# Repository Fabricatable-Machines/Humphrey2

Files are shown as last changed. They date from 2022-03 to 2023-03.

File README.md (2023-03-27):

# Humphrey2
A self replicating large format open hardware CNC router

*by Jens Dyvik, March 2022 - ongoing*

### Index

 - [Dev log](https://github.com/Fabricatable-Machines/Humphrey2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)
 - [Bill of materials](https://github.com/Fabricatable-Machines/Humphrey2#bom)
 - [FreeCAD source file](https://github.com/Fabricatable-Machines/Humphrey2/blob/main/humphrey2.FCStd)
 - [STEP export of assembly](https://github.com/Fabricatable-Machines/Humphrey2/blob/main/humphrey2-step-export.step)
 - [Files for CNC milling](https://github.com/Fabricatable-Machines/Humphrey2/tree/main/files-for-CNC-machining)
 - [Files for 3D printing](https://github.com/Fabricatable-Machines/Humphrey2/tree/main/files-for-3D-print)
 - [License](https://github.com/Fabricatable-Machines/Humphrey2#license)

### Dev log March 27th 2023 - Self-replication test and family tree

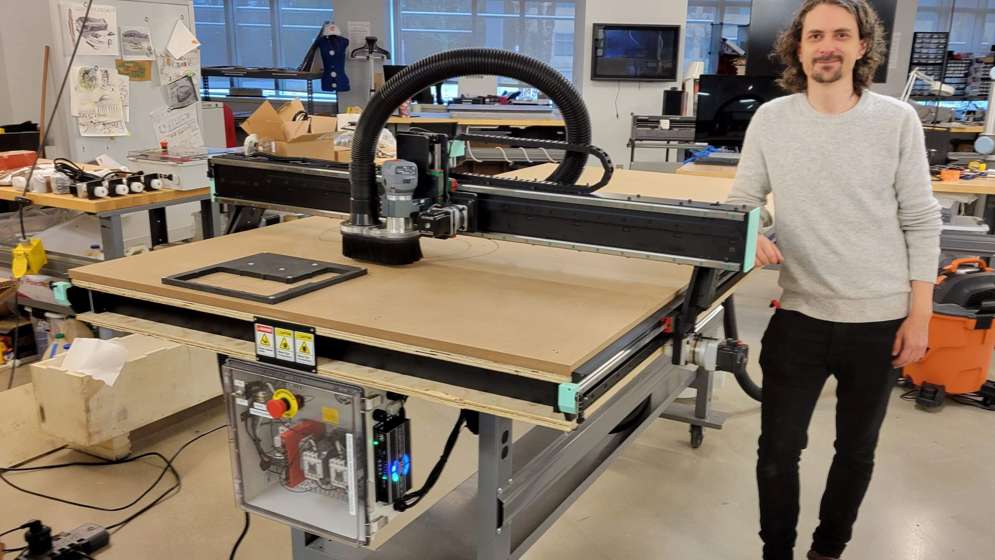
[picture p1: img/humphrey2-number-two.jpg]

*An assembled and operational Humphrey2 made on a Humphrey2*

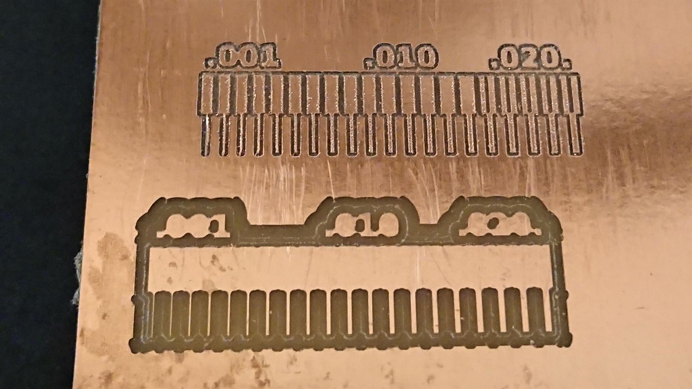
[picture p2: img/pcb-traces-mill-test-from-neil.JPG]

*Precicion test. Feature size in inches. Very low backlash and high repeatability. Unfortunately the only available 0.4mm end mill was broken, so the top traces are rough*


*The machine family tree so far. Three generations of machines making machines.*

### Dev log November 29th 2022 - Good test cuts and promising self-replication

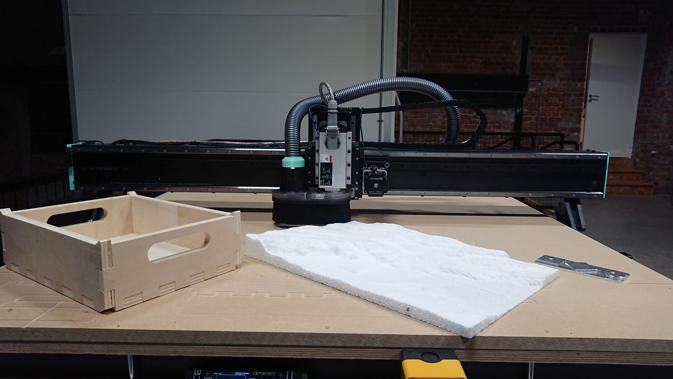
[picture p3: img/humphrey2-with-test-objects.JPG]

*15mm poplar plywood cut in one pass at 4200mm/m, 50mm styrofoam 3D milled and 8mm aluminium test pattern*

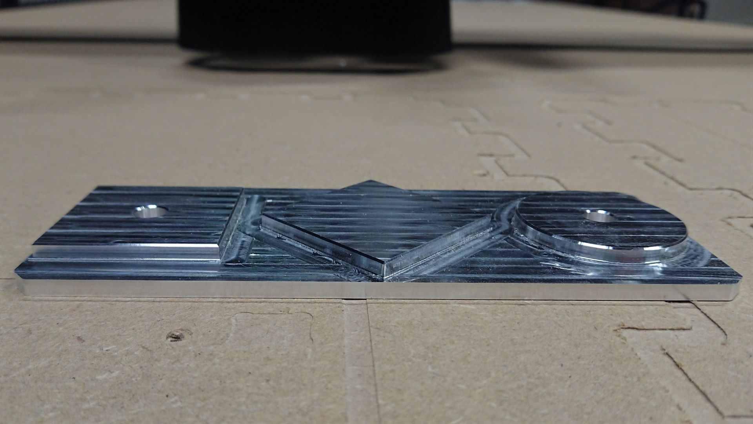
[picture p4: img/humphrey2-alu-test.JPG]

*Accuracy seems to be about +- 0.1mm. 6082 Aluminium cut with a 6mm single flute bit. 0.7mm pass depth, 1440mm/m feedrate + finish pass*

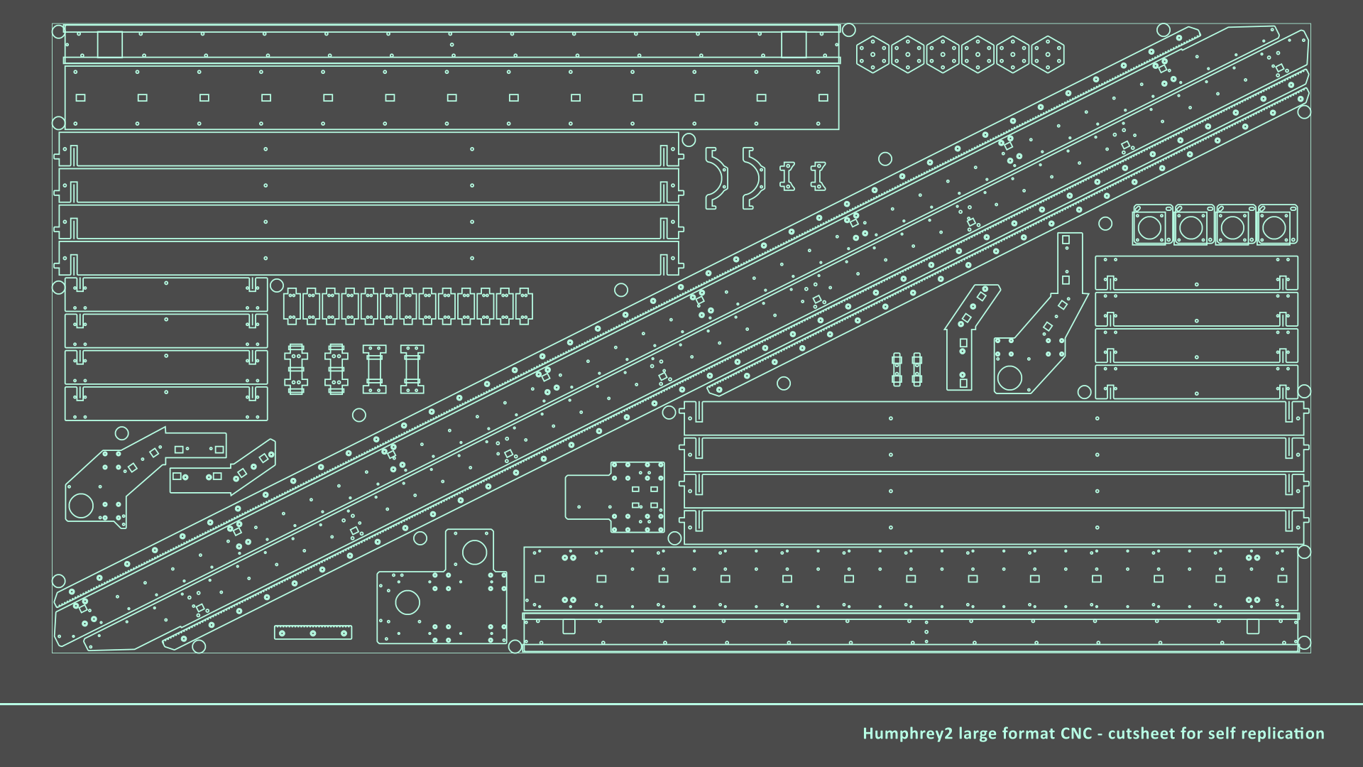
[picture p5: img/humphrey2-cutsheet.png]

*All phenolic parts for a Humphrey2 fit on one 2440mm x 1220mm x12mm sheet. The same size as the work area.*

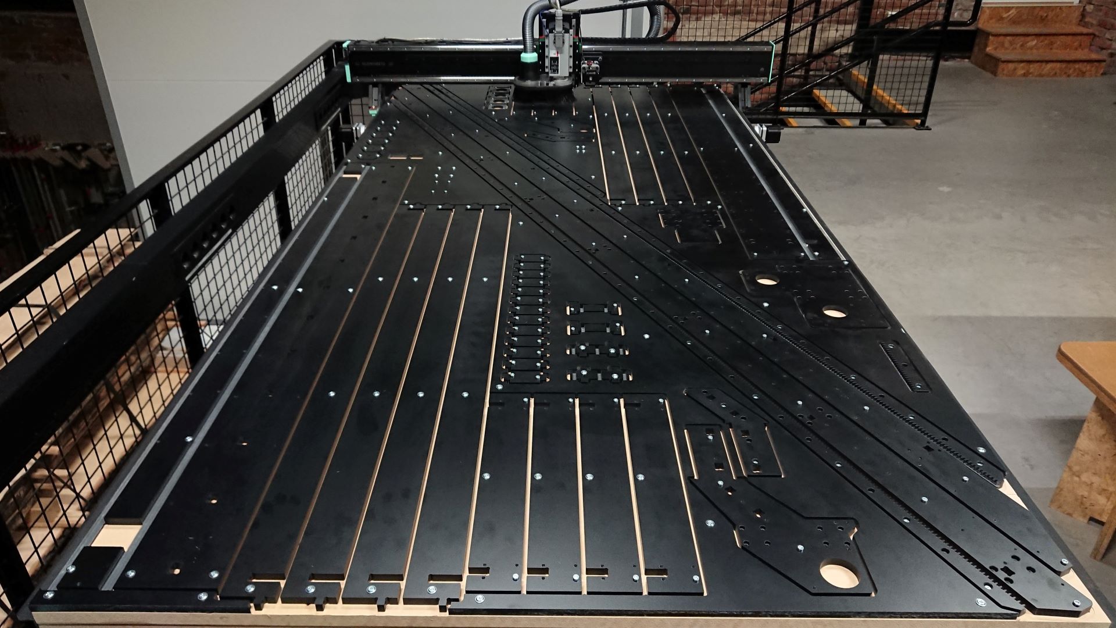
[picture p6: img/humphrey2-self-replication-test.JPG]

*Test milling of parts went well*

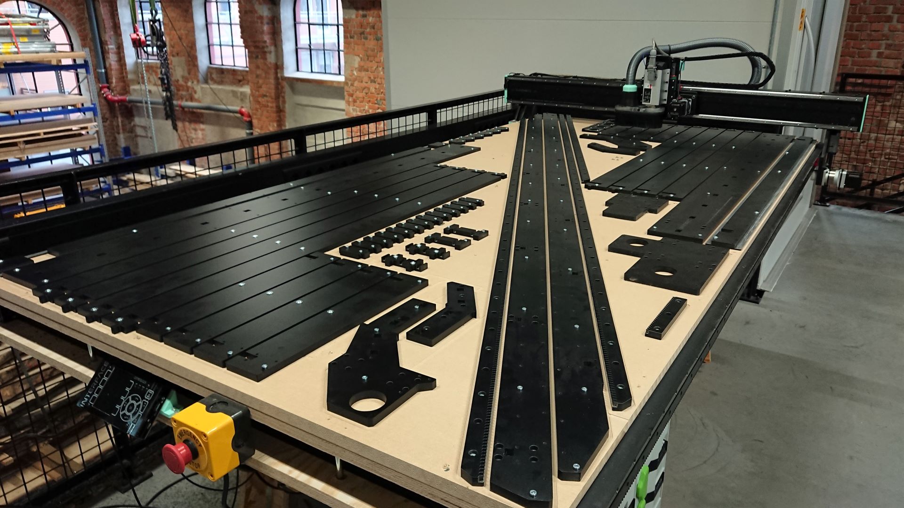
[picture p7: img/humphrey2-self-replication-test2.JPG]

*Cutsheet with all the leftover material removed. Note all the screws holding down each part allowing for a finish pass*

### Dev log October 31st 2022 - Smooth sailing for first test milling of parts and assembly

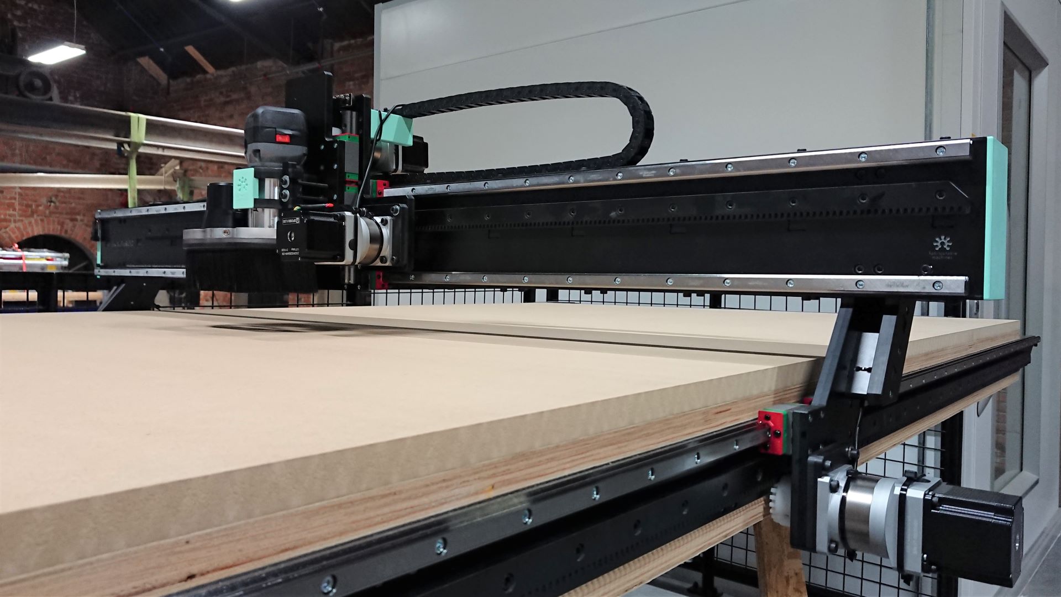
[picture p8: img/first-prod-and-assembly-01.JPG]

*Very few hickups during first assembly - next up lots of testing*

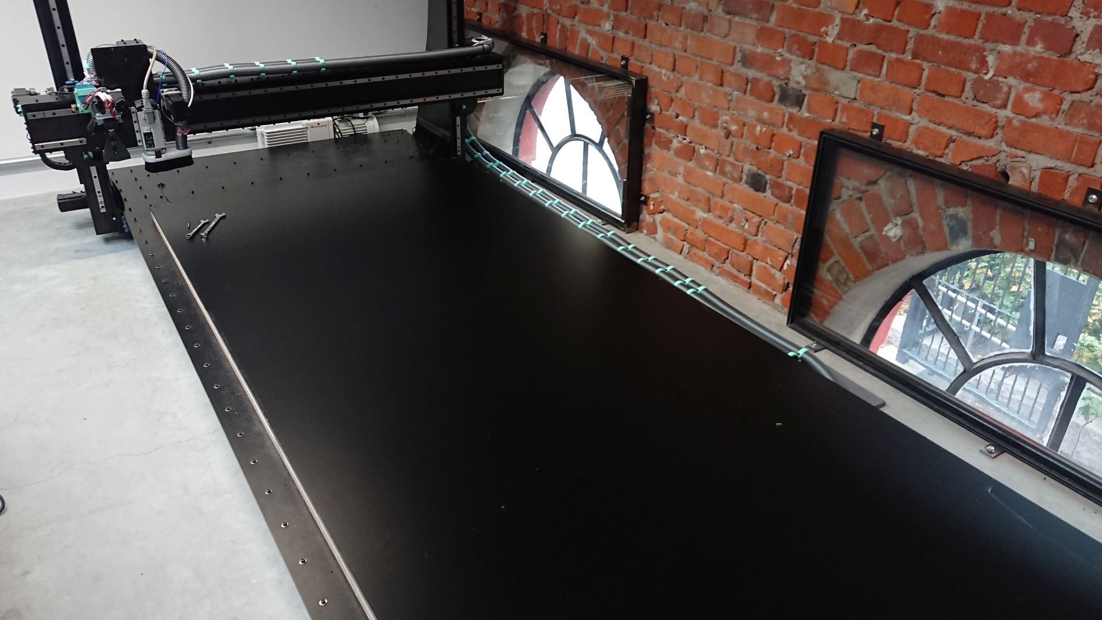
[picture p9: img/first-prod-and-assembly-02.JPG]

*Full size phenolic sheet loaded on [Hanzo](https://github.com/Fabricatable-Machines/Hanzo), ready to become Humphrey2 parts*

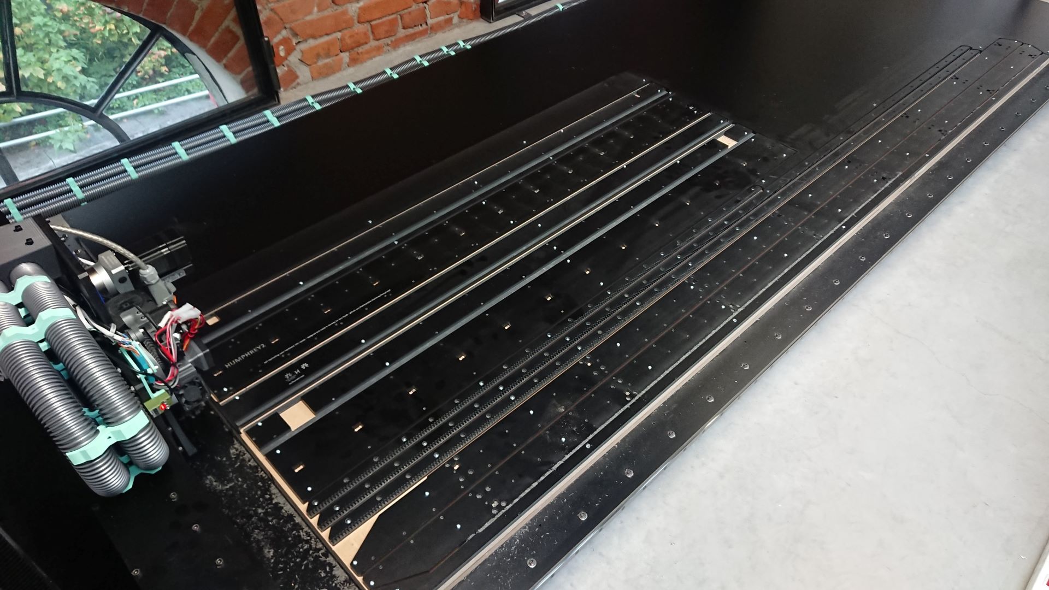
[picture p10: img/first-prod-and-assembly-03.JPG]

*It felt great to use [Hanzo](https://github.com/Fabricatable-Machines/Hanzo), a Fabricatable machine, to make another Fabricatable machine!*

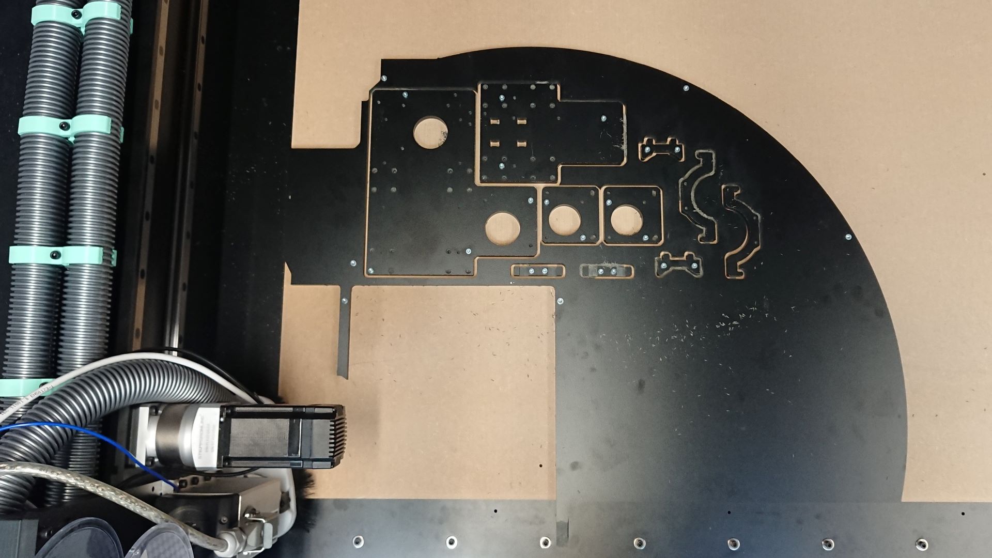
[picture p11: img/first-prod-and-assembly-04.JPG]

*Using leftovers to make X - Z assembly parts*

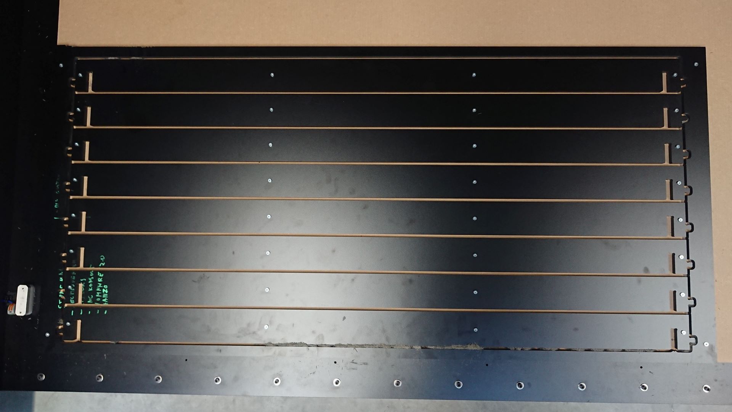
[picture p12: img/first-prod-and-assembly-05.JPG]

*The cross pieces were also milled from leftovers*

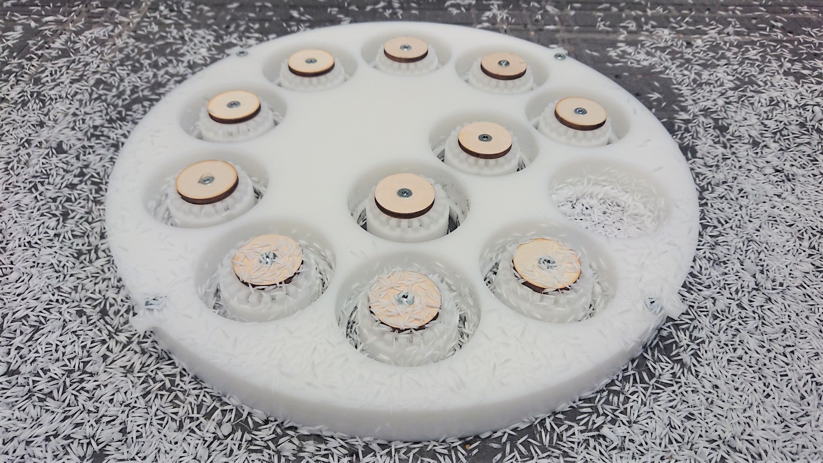
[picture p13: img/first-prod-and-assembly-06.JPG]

*Batch milling pinions from POM plastic leftovers*

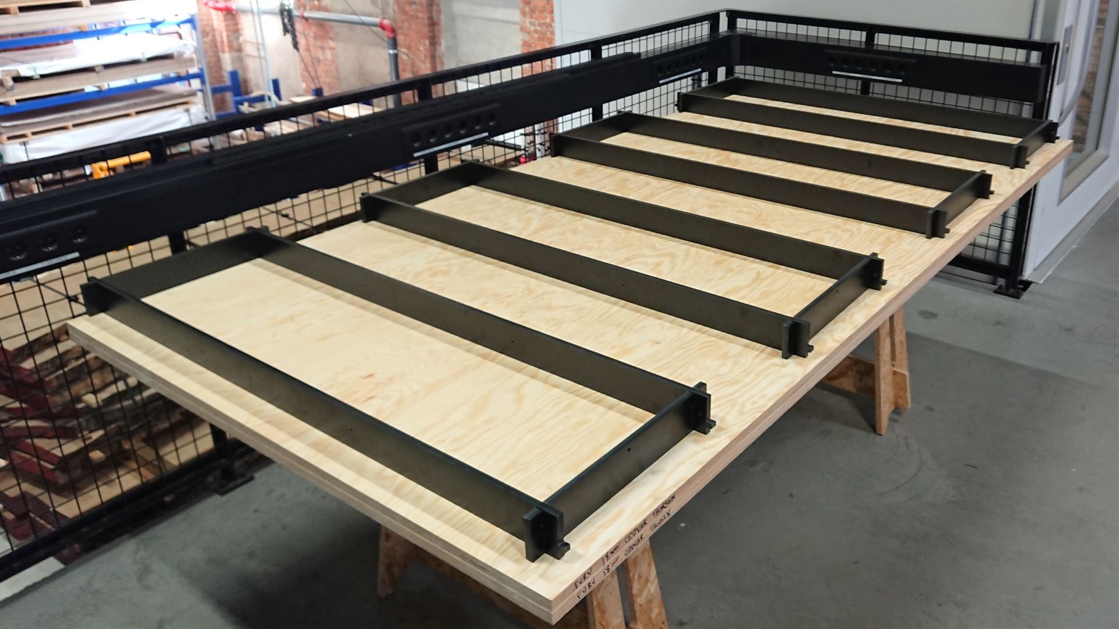
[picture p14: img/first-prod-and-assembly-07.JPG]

*The cross pieces ensure constant distance between the left and right X rail, and function as torsion box spacers*

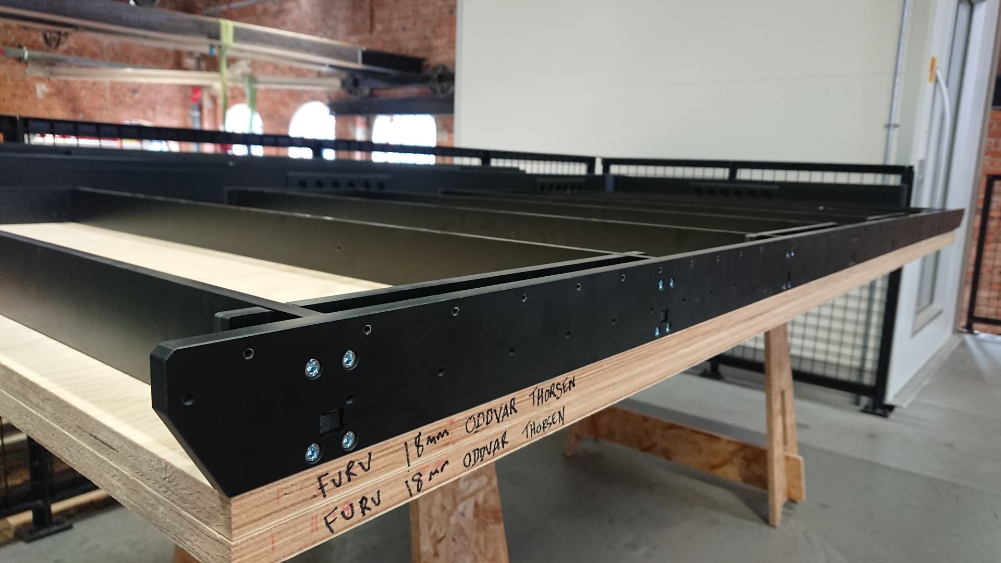
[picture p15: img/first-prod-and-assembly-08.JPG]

*All holes thread milled during production makes assembly fast*

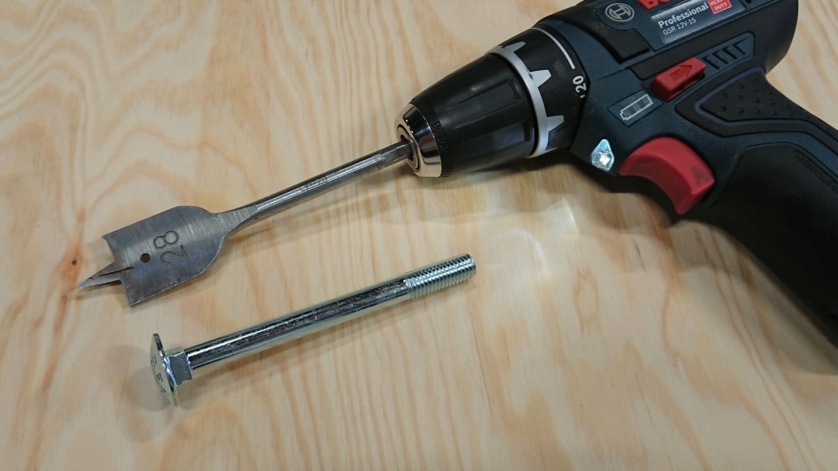
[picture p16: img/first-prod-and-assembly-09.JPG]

*Using a spade drill to counterbore the carriage bolt holes*

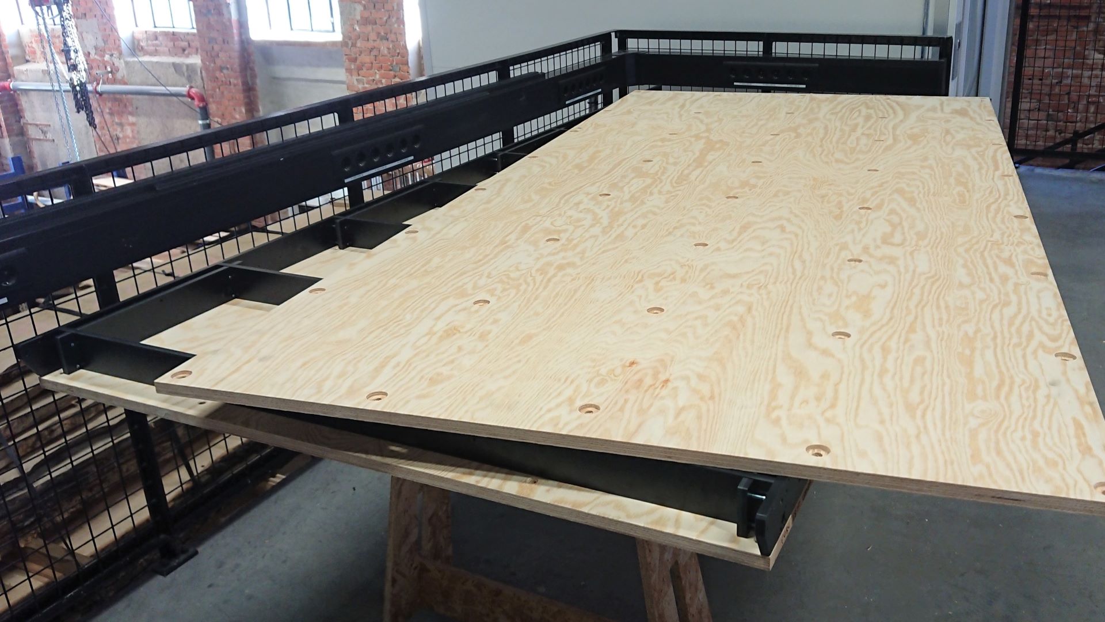
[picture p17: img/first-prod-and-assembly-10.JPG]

*The two plywood sheets that make up the top and bottom torsion box skin of the bed can be drilled manually on site. This makes for cheaper and easier shipping of the milled parts.*

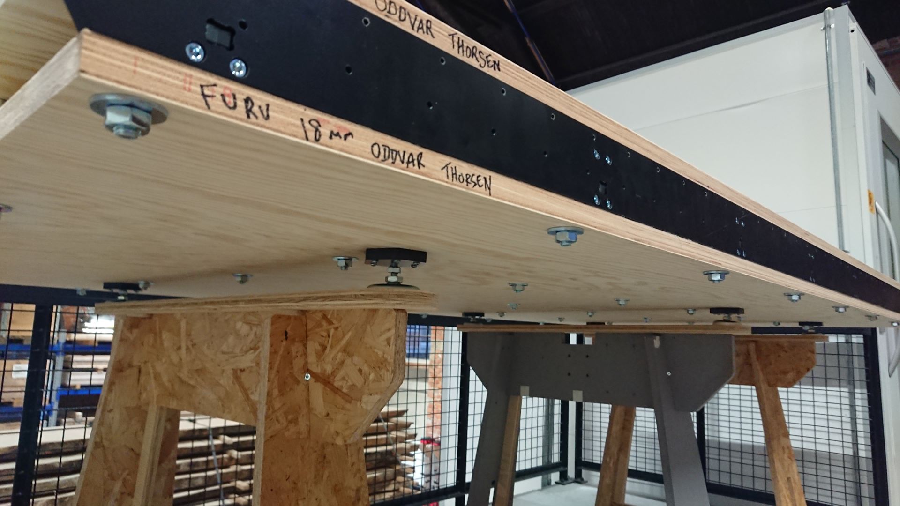
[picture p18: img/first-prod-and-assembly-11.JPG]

*The adjustable feet enable leveling. What kind of sawhorse or legs to use is open.*

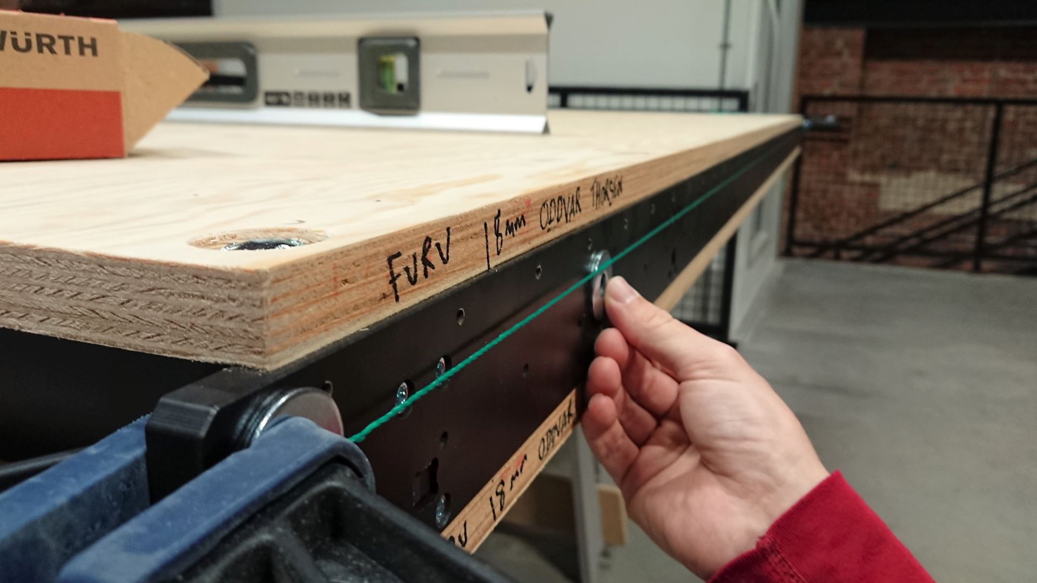
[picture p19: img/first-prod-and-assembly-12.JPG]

*Using masonry thread and three washers to make the outer walls carrying the X rails as straight as possible. As spirit level is used to try to make the assembly flat.*

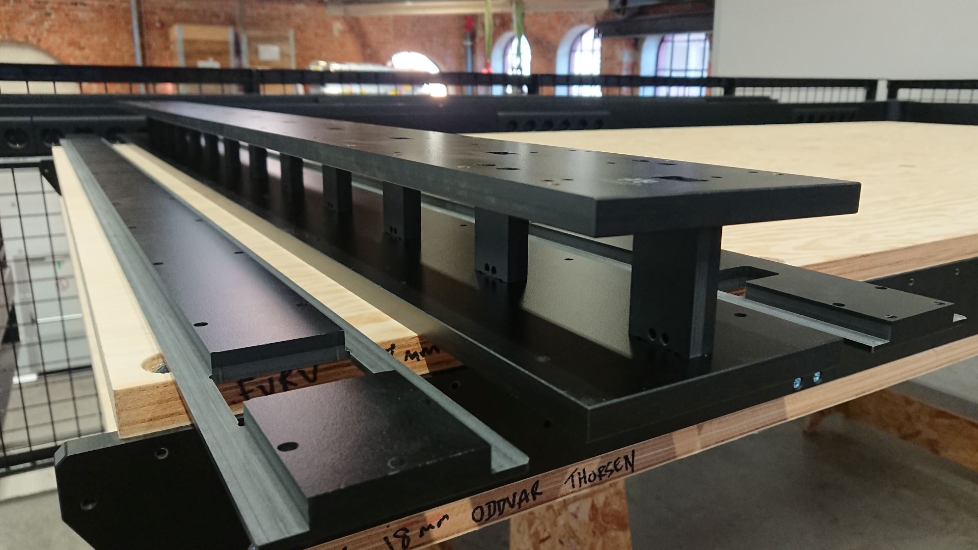
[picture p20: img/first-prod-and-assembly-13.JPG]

*The gantry has spacer nuts so shorter screws can be used*

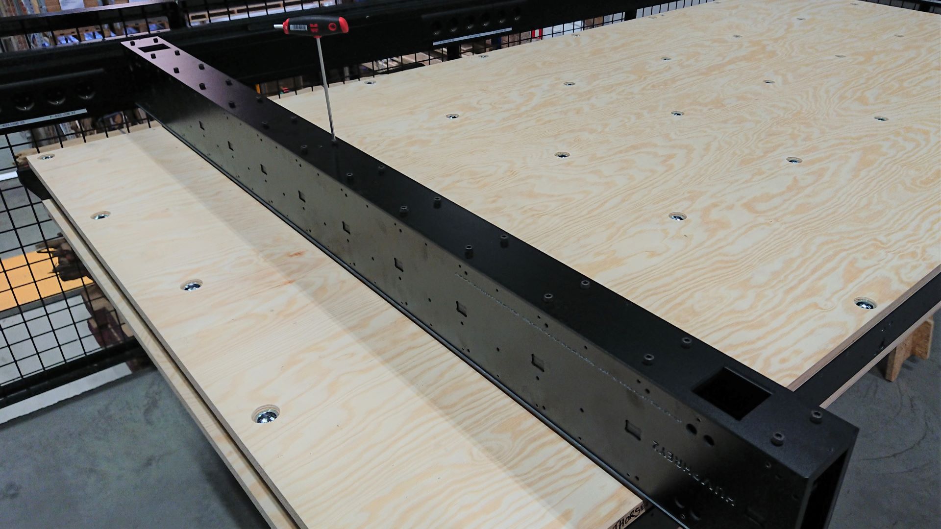
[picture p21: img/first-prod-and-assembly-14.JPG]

*Again, all holes thread milled during manufacturing makes assembly super fast*

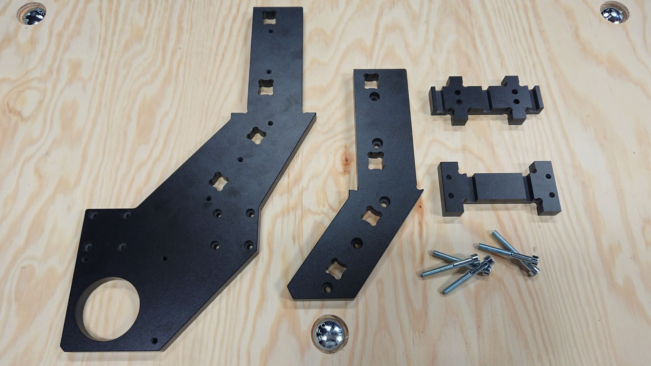
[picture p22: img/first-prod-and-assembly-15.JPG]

*Gantry feet parts*

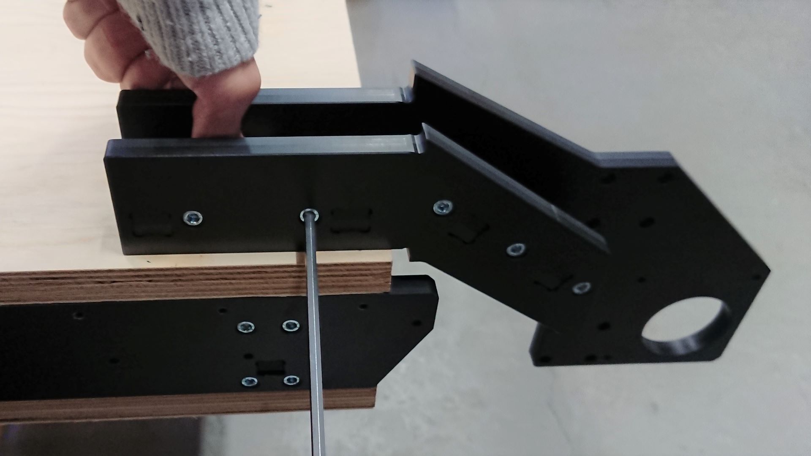
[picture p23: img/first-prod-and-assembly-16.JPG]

*Tightening under pressure*

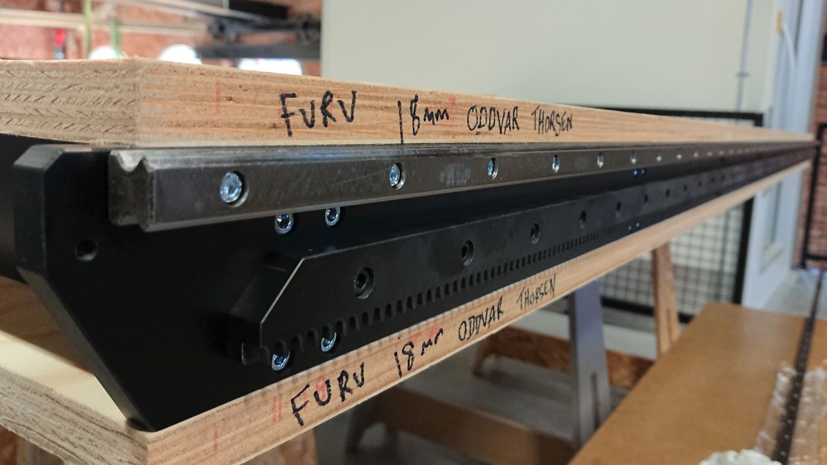
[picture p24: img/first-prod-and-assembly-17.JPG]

*Mounting rails and racks*

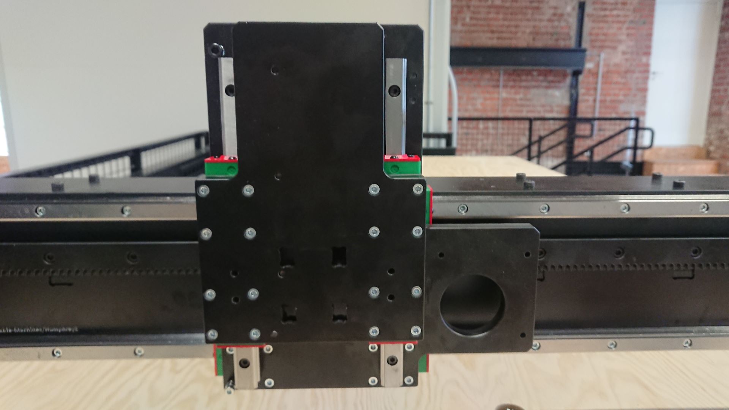
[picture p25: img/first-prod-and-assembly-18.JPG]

*Mounting the X-Z carriage*

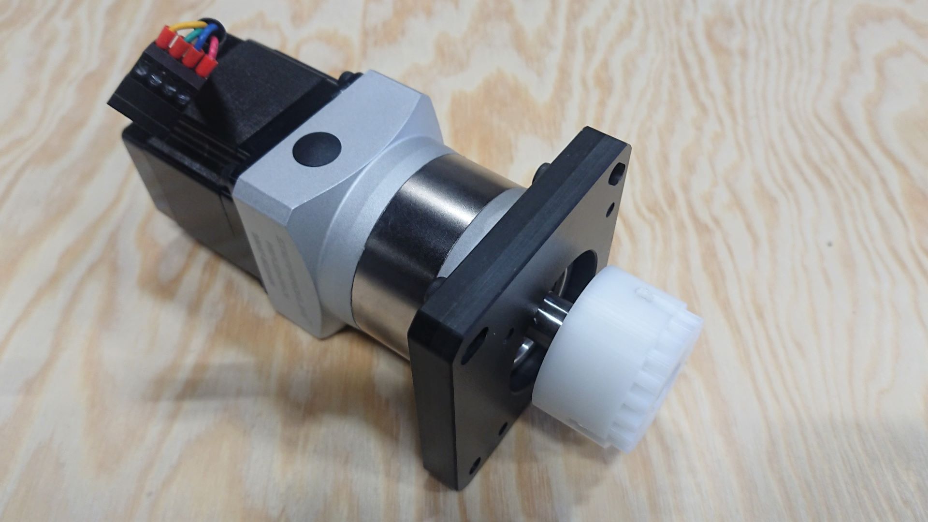
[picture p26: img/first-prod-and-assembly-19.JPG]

*Mounting gearboxes to the steppers and pinion and motor plates to the gearboxes*

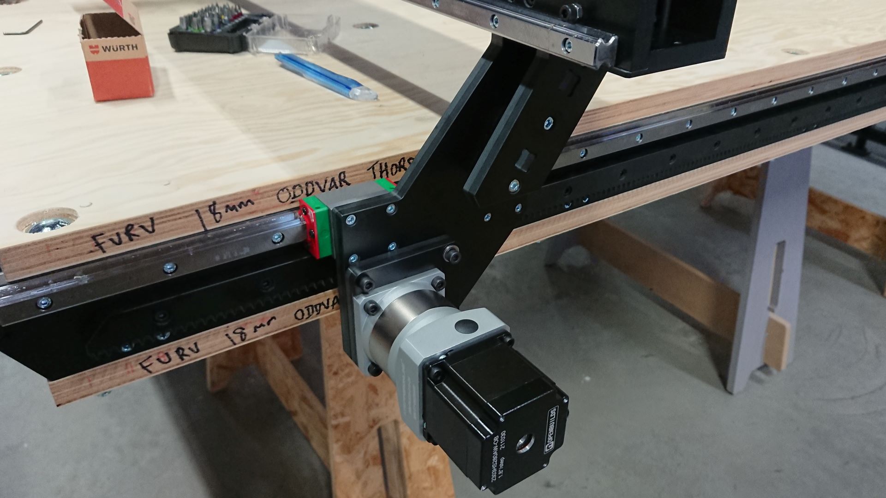
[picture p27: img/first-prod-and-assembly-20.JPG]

*Gantry detail. The pinions should be snug but not too tight against the racks.*

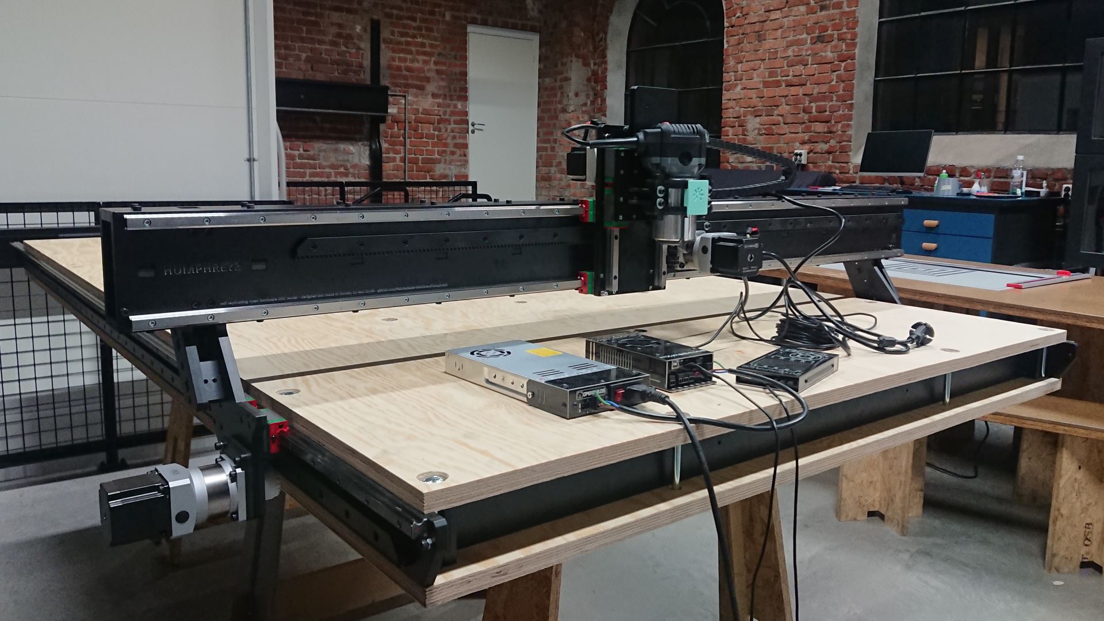
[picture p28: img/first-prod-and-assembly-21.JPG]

*Preparing for electronics work. I am testing the OpenBuilds Blackbox and Interface for fast and easy wiring.*

### Dev log October 4th 2022 - Nesting done + design tweaks

Next up; machining, assembly and testing!

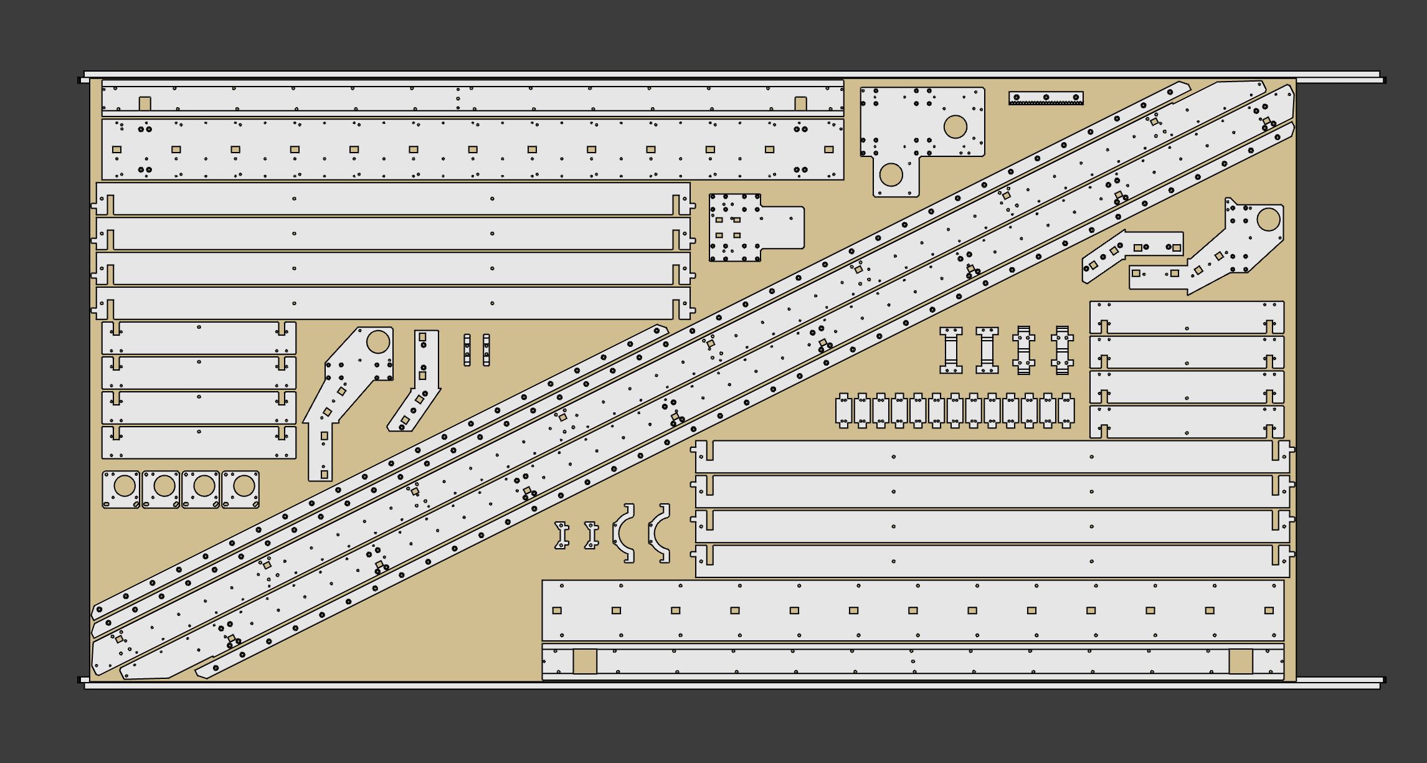
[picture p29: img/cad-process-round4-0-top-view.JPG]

*59 parts to machine from phenolic resin composite, all from a single cutsheet*

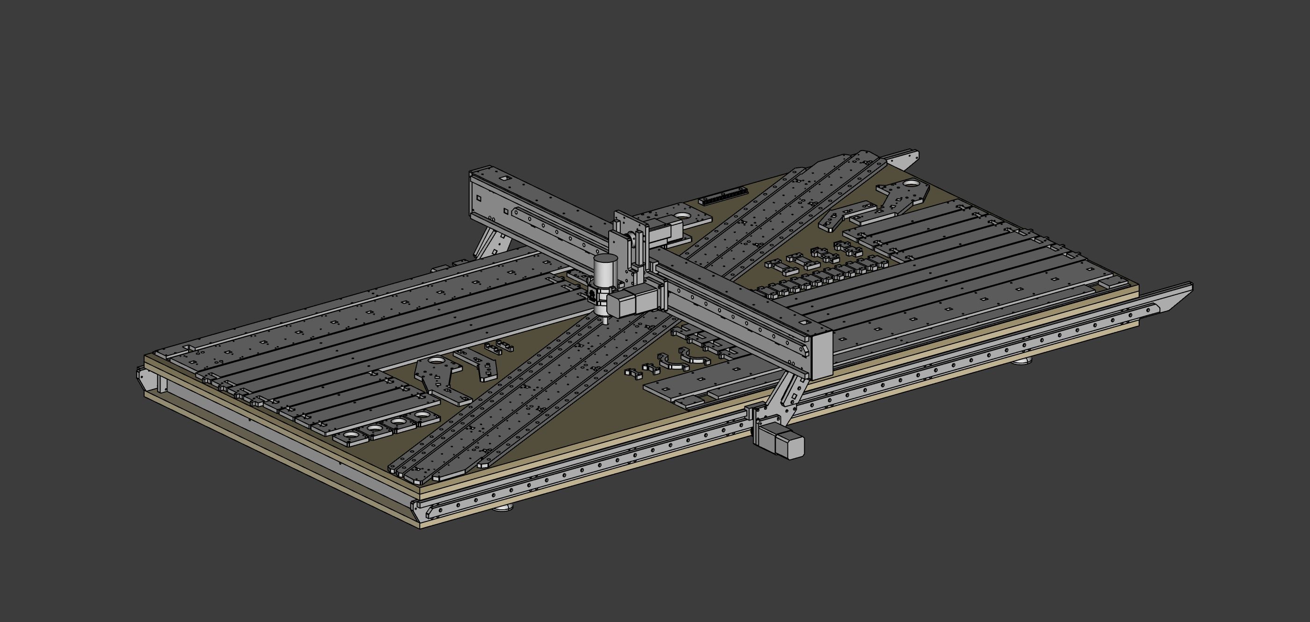
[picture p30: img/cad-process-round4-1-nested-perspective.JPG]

*Portrait of a self replicating machine*

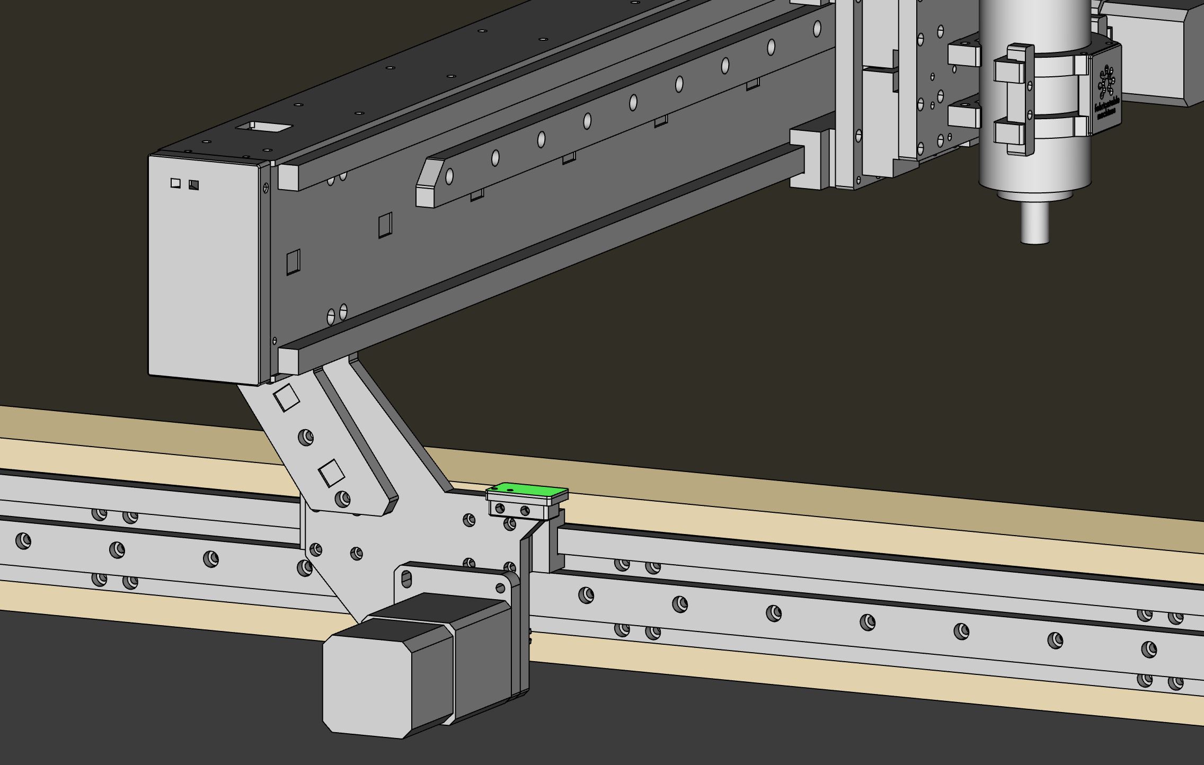
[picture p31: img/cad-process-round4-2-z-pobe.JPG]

*Added probe plate for Z axis probing of bit length*

### Dev log September 9th 2022 - Initial design is done!

Finally the first version of the design is done. The FreeCAD model is fully parametric, which feels great. So it is possible to change parameters like material thickness, tolerances, clearance between the gantry and the bed and so on without breaking the model. Next up is test milling some parts and maybe do some parameter tuning before milling all the parts for the first prototype!

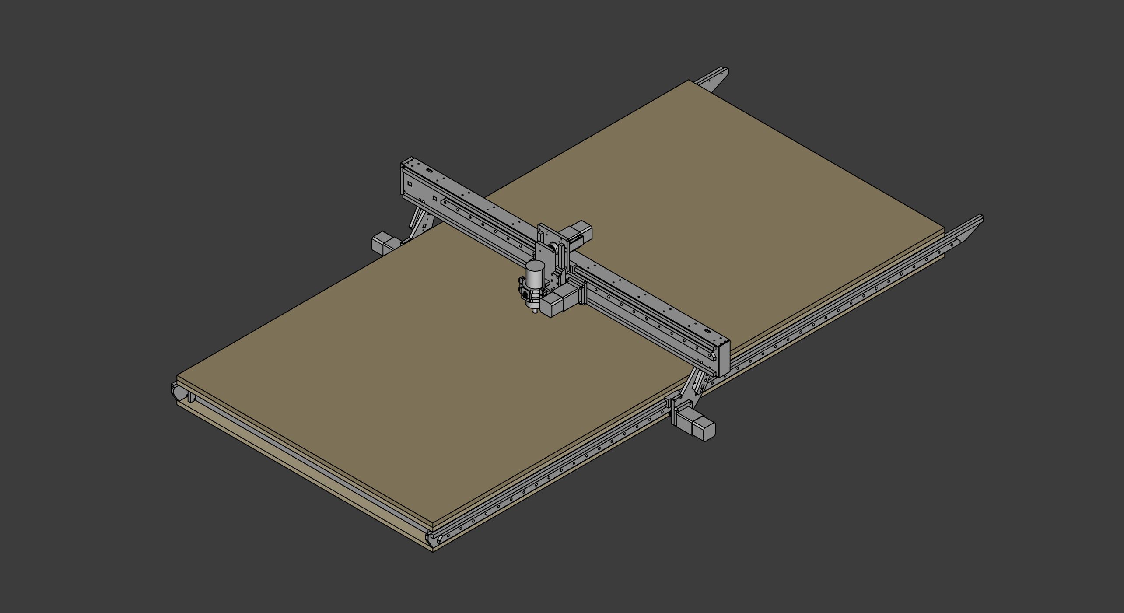
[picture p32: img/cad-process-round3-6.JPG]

*Proportions feel good*

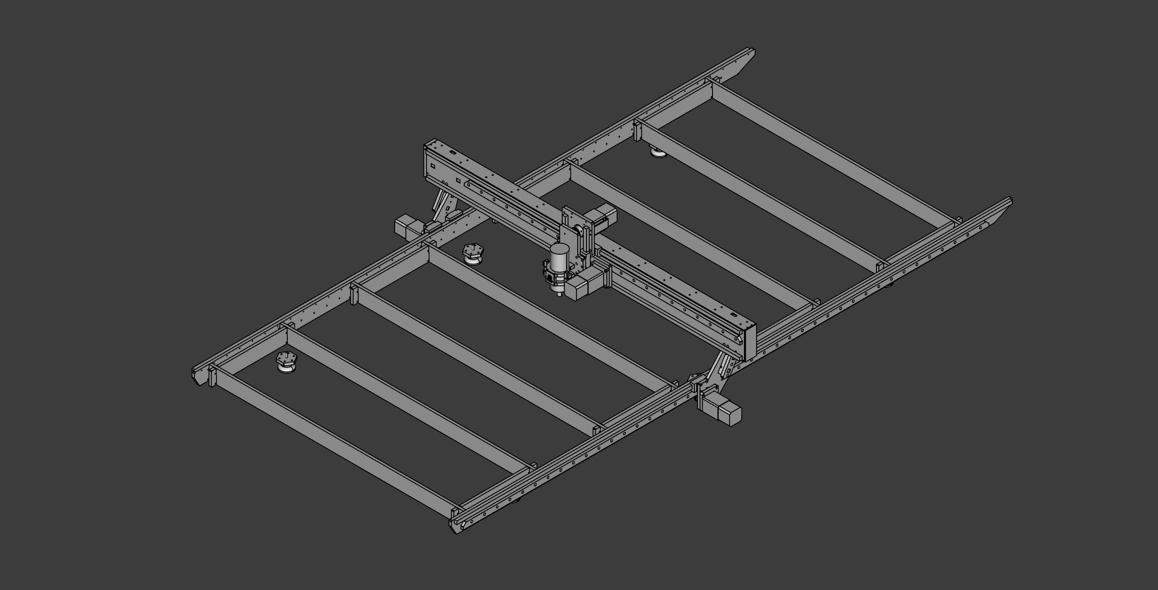
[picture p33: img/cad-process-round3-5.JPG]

*The skeleton without the plywood torsion box skins and the sacrificial MDF layer*

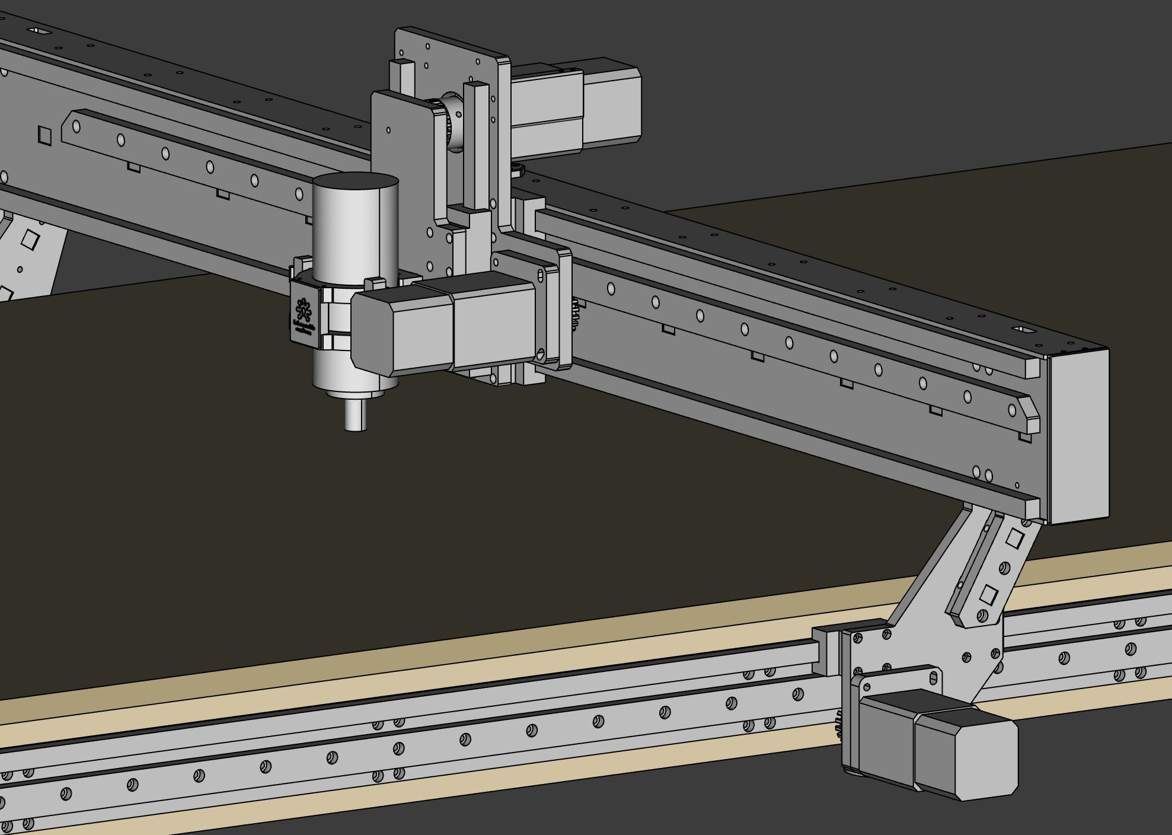
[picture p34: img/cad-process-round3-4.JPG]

*Close up of the gantry and XZ axis*

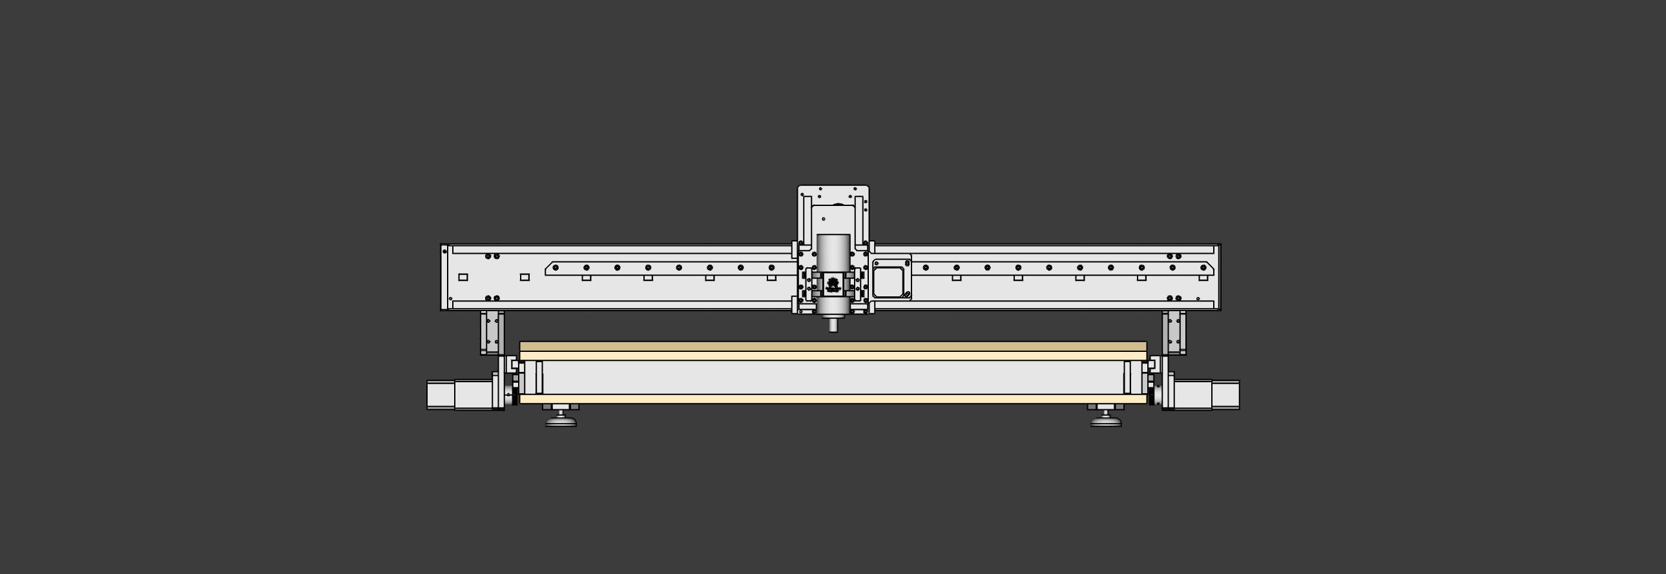
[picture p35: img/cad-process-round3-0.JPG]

*Front view*

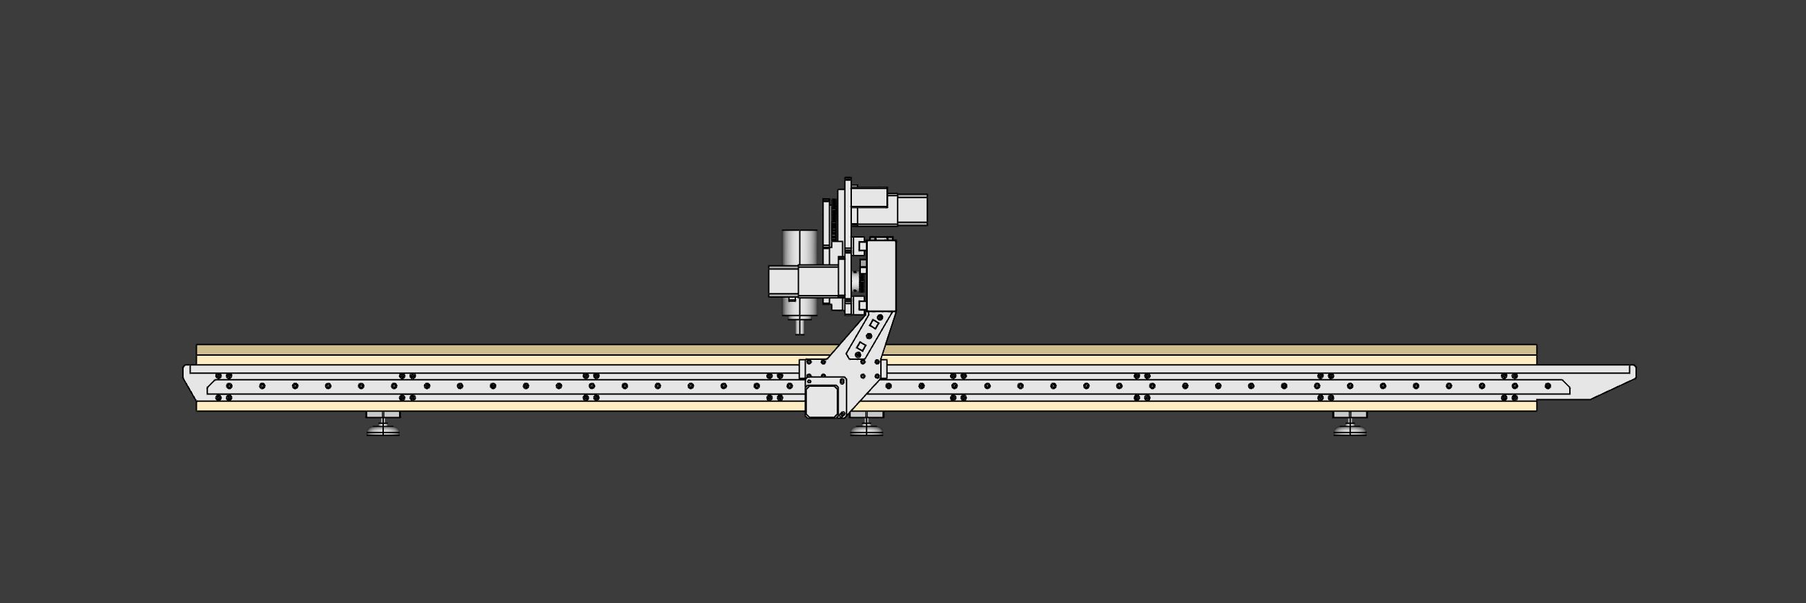
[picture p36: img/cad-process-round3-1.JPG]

*Side view*

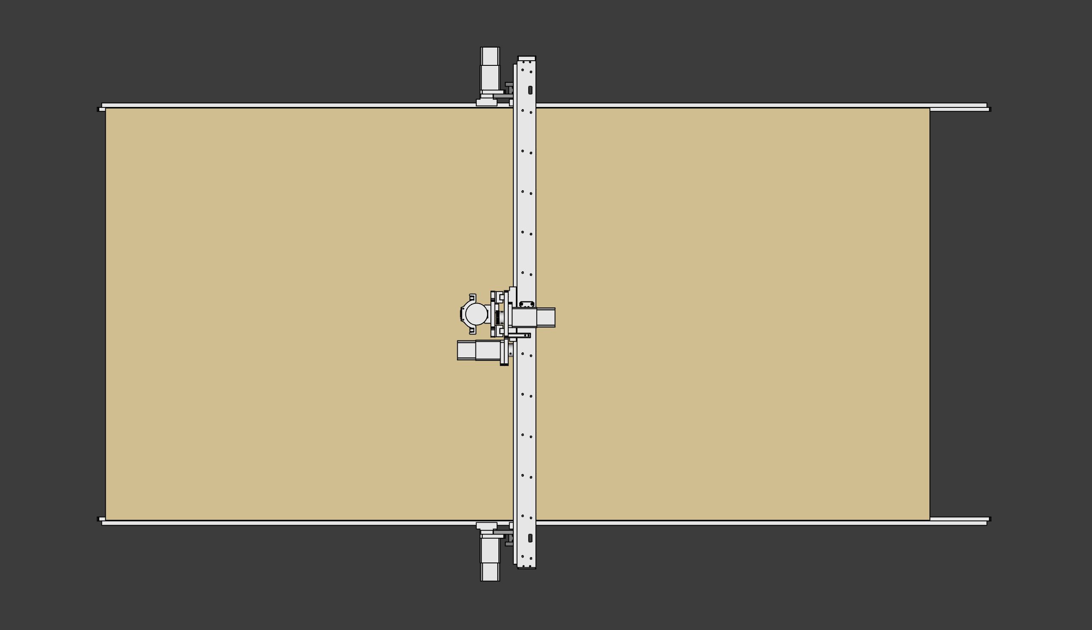
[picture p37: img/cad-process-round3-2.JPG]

*Top view*

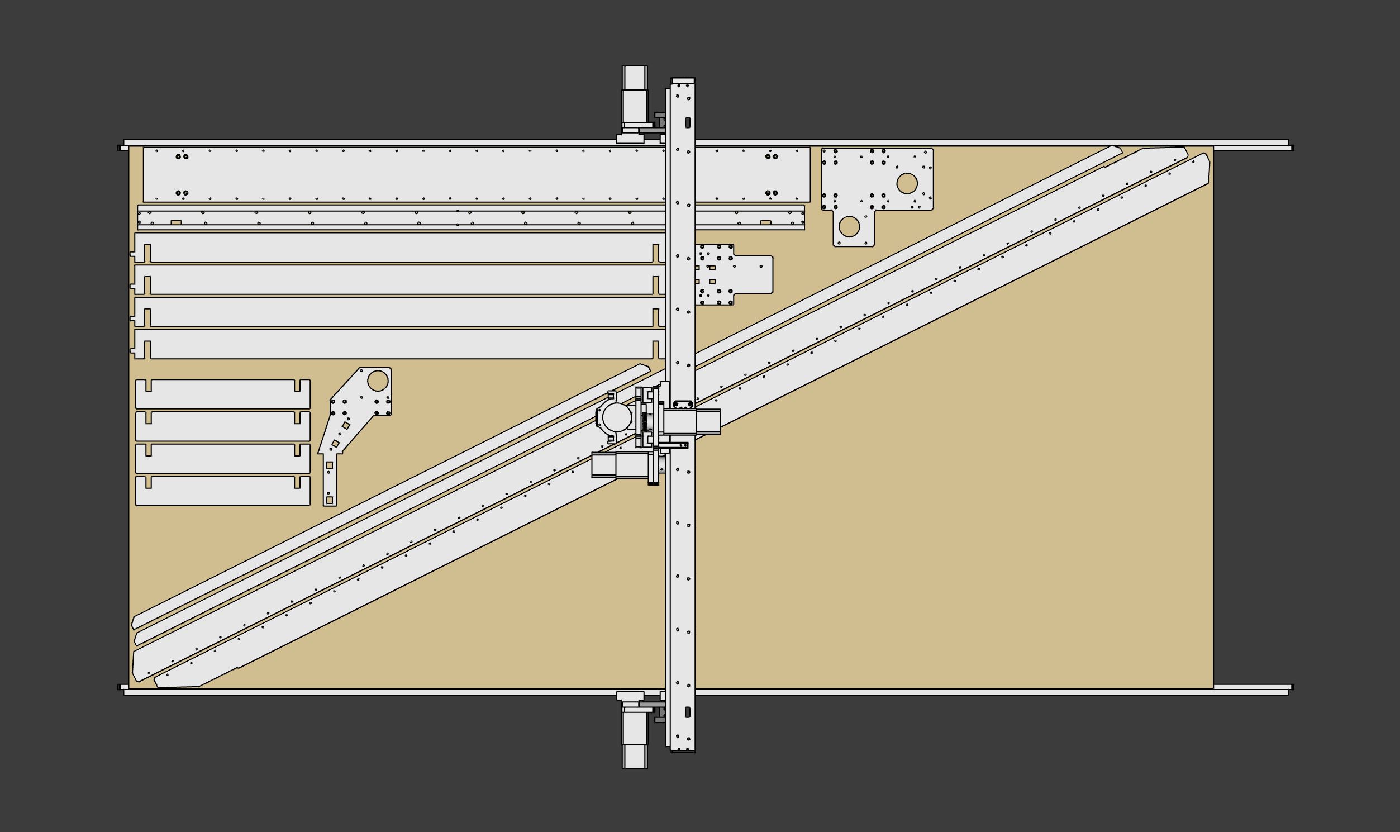
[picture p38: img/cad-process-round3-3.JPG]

*A rough nesting test indicates that all the milled parts will fit on one cutsheet as planned!*

### Dev log August 2022 - CAD progress and a FreeCAD bug

The master CAD design is progressing slow and steady. I ran into a bug with FreeCAD expressions *(reported [here](https://forum.freecadweb.org/viewtopic.php?f=3&t=71309&p=620375#p620375))*, so I have reverted to using FreeCAD version 19 for now. It has been nice to use the relatively new FreeCAD Link feature to make a simple assembly by embedding the external rack and pinion file. Saving both computation time and storage space :)

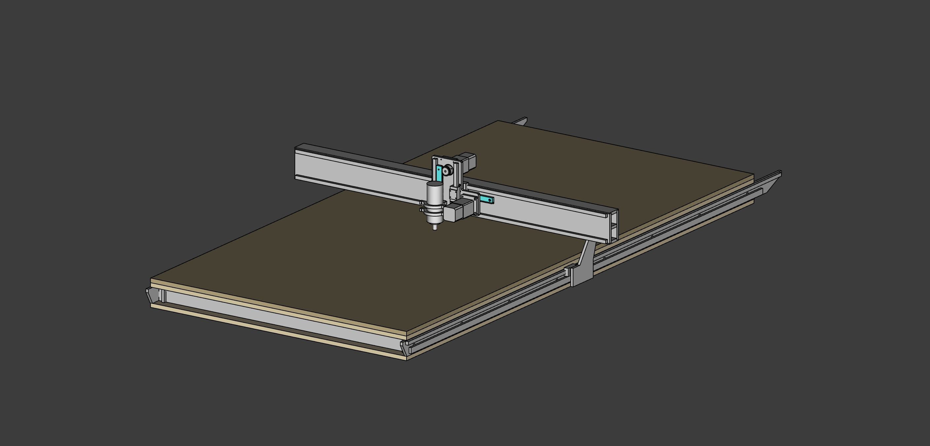
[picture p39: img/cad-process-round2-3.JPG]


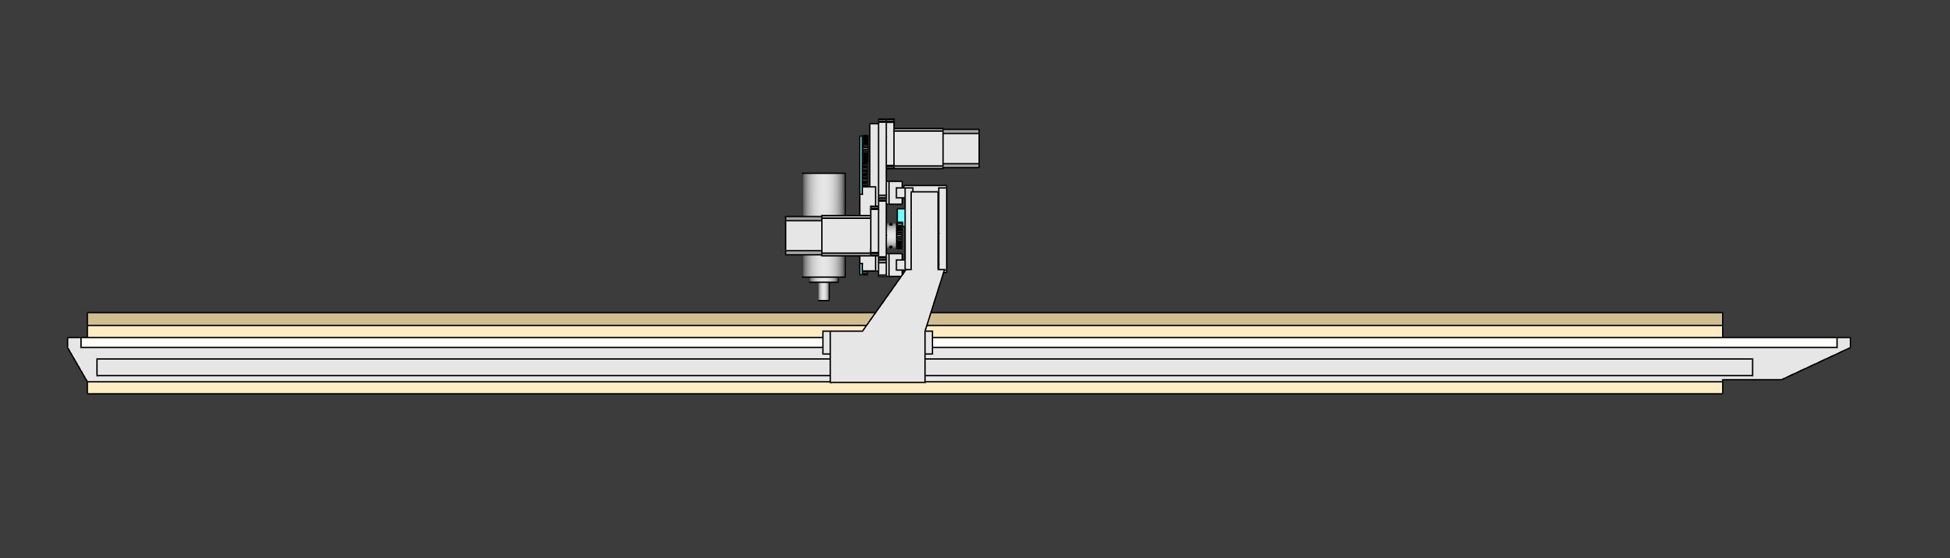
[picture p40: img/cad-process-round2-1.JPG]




### Dev log June 2022 part2 - Starting the CAD master design file

I have started making the proper design file in Freecad. The work in progress file is published and reguraly updated [here](https://github.com/Fabricatable-Machines/Humphrey2/blob/main/humphrey2.FCStd).


Work in progress phenolic skeleton


I am nesting the parts onto the bed of the machine as I go. The goal is to be able to cut all critical parts from one cutsheet.


Plywood above and below the skeleton makes up the torsion box. The top layer is a MDF plate as a scarafical layer


Test nesting onto the bed of the 3D model.

### Dev log June 2022 - Testing construction principles and components


In order to test design ideas, I decided to make a 1:1 test of a small cutout section of the machine bed


The [Hanzo](https://github.com/Fabricatable-Machines/Hanzo) machine that I developed and built is now operatoinal. It feels great to use one fabricatable machine to make the parts for the next one!


Cutsheet for the phenolic resin cardboard composite test parts.


The plywood edges came out super clean and straight on Hanzo, using a 6mm compression cutter in two passes.


The phenolic pieces screw together with tapped holes.


Testing to use a marker to mark positions for pre drilled holes. I want avoid having to CNC machine the 2440mm x 1220mm plywood sheets.


Drilling the plywood sheets by hand will mitigate the need for shipping plywood sheets with the phenolic machine parts, instead they can be sourced locally.


100mm wood screws will lock the torsion box bed together.


The [CNC friendly](https://github.com/fellesverkstedet/fabricatable-machines/wiki/Modules#cnc-friendly-rack-and-pinion) rack screws into the side wall with quite tight tolerances.


A 15mm linear rail mounts above the rack into tapped holes.


Milling a [CNC friendly](https://github.com/fellesverkstedet/fabricatable-machines/wiki/Modules#cnc-friendly-rack-and-pinion) pinion in POM on [Hanzo](https://github.com/Fabricatable-Machines/Hanzo).


First test assembled. I have mixed feelings about the flexure that ensure constant preload between the pinoin and the rack.


A second test with a more classic adjustable motorplate instead of flexures.

**Notes from making and testing:**

 - Tolerance for milled sides needs to be bigger.
 - Leading chamfer/fillets for slots will help in assembly.
 - Tapping though 12mm material with4 tap diffiult. Note for screw length.
 - Outer wall can be mounted upside down. Hoka poka.
 - 100mm screws are easy to get very skew.
 - A flexure at 60x4mm dimension is much too stiff. 60x2mm seems promising.
 - The flexure vibrates a bit at higher speeds.
 - Not enough space for indents in pinion that show set screw hole drill positions. 3 tabs can do the same job.
 - Cut depth of pinion teeth reduced to 5.6mm because of available 2mm bit flute lengths
 - Inside hole set to 14.05mm. Premilled to ø 13.6, then ran three times at ø14.05mm with a long 5deg ramp continuous to the bottom. Still the bottom of the hole became too small. Maybe reduce thickness of stock?
 - Motorplate with three screws instead of flexures feels safer and more suitable.
 - Openbuilds controller and interface is easy to work with.

### Dev log March 2022 - early sketches







### BOM
*Work in progress*

The [spreadsheet file](https://github.com/Fabricatable-Machines/Humphrey2/blob/main/BOM-Humphrey2.xls) has links to European and US vendors.



### License

Creative Commons Attribution-ShareAlike
http://creativecommons.org/licenses/by-sa/4.0/

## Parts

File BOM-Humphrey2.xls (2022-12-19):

BOM Humphrey2
Work in progress december 2022, not yet finalized
All prices in USD excluding local VAT
Product type | Product name | Option | Cost USD | Quantity | Transportation and customs clearance | Total cost with transport and import | Part no | Vendor (Europe) | Link (Europe) | US alternative
Bearing block | HGH15CAZAC | 15mm high and narrrow, light preload | 29.36 | 12 |  | 352.32 |  | CNC store EU | https://www.cnc-store.eu/ | https://motionconstrained.com/
Precut linear rail | HGH15 | 15mm type, mounting from above, length 2620mm, 20mm to first bore | 172.5 | 2 |  | 345 |  | CNC store EU | https://www.cnc-store.eu/ | https://motionconstrained.com/
Precut linear rail | HGH15 | 15mm type, mounting from above, length 1480mm, 20mm to first bore | 96 | 2 |  | 192 |  | CNC store EU | https://www.cnc-store.eu/ | https://motionconstrained.com/
Precut linear rail | HGH15 | 15mm type, mounting from above, length 220mm, 20mm to first bore | 26 | 2 | 250 | 302 |  | CNC store EU | https://www.cnc-store.eu/ | https://motionconstrained.com/
Oil for linear rail maintenance |  |  | 6 | 1 |  | 6 |  | McMaster | https://www.mcmaster.com/8710T697/
Phenolic resin cardboard compostie | Formica compact | 12mm | 330 | 1 |  | 330 |  | Fritzøe | https://www.fritzoeengros.no/produkter/interioer/dekor/formica | https://www.richlite.com/ |  | https://accurateplastics.acculam.com/item/xx-paper-phenolic-laminates/phenolkraft-xx-laminate-sheet-48-x-96-/item-3128
Plywood | Softwood | 19mm | 80 | 2 |  | 160 |  |  | https://www.fritzoeengros.no/kategori/kryssfiner/ubehandlet-kryssfiner/furu | https://www.homedepot.com/p/Cabinet-Grade-Plywood-Panel-Common-23-32-in-x-4-ft-x-8-ft-Actual-0-688-in-x-48-in-x-96-in-1077486/302610611
MDF | Regular | 19mm | 50 | 1 | 130 | 180 |  | Fritzøe | https://www.fritzoeengros.no/produkter/mdf-og-spon | https://www.homedepot.com/p/3-4-in-x-4-ft-x-8-ft-MDF-Panel-D11612490970000/304325742
Sawhorses (machine legs) | 42.4"W x 28.8"H C550 Powder-Coat Steel Sawhorse and Jobsite Table with 1100 lb capacity |  | 50 | 3 |  | 150 |  | Home depot |  | https://www.homedepot.com/p/TOUGHBUILT-42-4-W-x-28-8-H-C550-Powder-Coat-Steel-Sawhorse-and-Jobsite-Table-with-1100-lb-capacity-TB-C550/205870368
Planetary gearbox | Helical Gear Nema23 Planetary Gearbox High Precision | 10:1, 6,35mm shaft | 59 | 4 | 135 | 371 |  | Stepper online | https://www.omc-stepperonline.com/ple-series-planetary-gearbox-gear-ratio-10-1-backlash-15-arc-min-for-6-35mm-shaft-nema-23-stepper-motor-ple23-g10-d6
Materials and linear rails total |  |  |  |  |  | 2388.32
CNC electronics bundle | Openbuilds Blackbox + Interface and more | Regular NEMA23 stepper motors + Interface CNC touch | 667 | 1 |  | 667 |  | Openbuilds | https://openbuildspartstore.com/cnc-electronics-bundle/
Router with ER11 collets | Router11 |  | 150 | 1 |  | 150 |  | Openbuilds | https://openbuildspartstore.com/router11/
Dust shoe |  | For Router11 | 160 | 1 |  | 160 |  | Openbuilds | https://openbuildspartstore.com/dust-shoe-for-routers/
E-chain | Drag Chain Cable Carrier | 1000mm | 16 | 1 | 100 | 116 |  | Openbuilds | https://openbuildspartstore.com/drag-chain-cable-carrier/
110v extension for spindle?
Spindle mount 65mm |  |  | 80 | 1 | 20 | 100 |  | Carbide 3D | https://shop.carbide3d.com/collections/accessories/products/shapeoko-hd-65mm-spindle-mount
Safety relay | G9SE-201 |  | 220 | 1 |  | 220 |  | Digikey | https://www.digikey.no/en/products/detail/omron-automation-and-safety/G9SE-201/7495167
E-stop | Minimum 2NC | Panel mount | 74 | 1 |  | 74 |  | Digikey | https://www.digikey.no/en/products/detail/omron-automation-and-safety/A22E-M-03/4076540
Sticker/label for e-stop |  |  |  |  |  |  |  | McMaster | https://www.mcmaster.com/6741K72/
Warning sticker – eyes |  |  |  |  |  |  |  | McMaster | https://www.mcmaster.com/5948T921/
Warnring sticker – ears |  |  |  |  |  |  |  | McMaster | https://www.mcmaster.com/5948T911/
Warning sticker – hands |  |  | 11.5 | 1 |  | 11.5 |  | McMaster | https://www.mcmaster.com/5891T49/
Power switch |  | Panel mount | 15 | 1 |  | 15 |  | McMaster | https://www.mcmaster.com/7343K771/
Reset button |  | Panel mount | 7 | 1 |  | 7 |  | Digikey | https://www.digikey.no/en/products/detail/e-switch/PV1S640NN/4028686
Circuit breaker |  |  | 25 | 1 |  | 25 |  | Digikey | https://www.digikey.no/en/products/detail/carlo-gavazzi-inc/GSB632PC16/9520312
Contactors | 3 pole with helper NC and NO |  | 49 | 2 |  | 98 |  | Digikey | https://www.digikey.no/en/products/detail/carlo-gavazzi-inc/CC12SD24/9485726
Power cable – in |  |  | 15 | 1 |  | 15 |  | Digikey | https://www.digikey.no/en/products/detail/tensility-international-corp/11-00122/12324951
Extension cord – for router |  |  |  | 1 |  | 0
USB type B socket |  |  | 18 | 1 |  | 18 |  | Digikey | https://www.digikey.no/en/products/detail/molex/0847300010/2790410
USB type B cable |  |  | 20 | 1 |  | 20 |  | Digikey | https://www.digikey.no/en/products/detail/te-connectivity-amp-connectors/1487594-1/6042822
DIN rail end stop? |  |  | 1.6 | 6 |  | 9.6 |  | Digikey | https://www.digikey.no/en/products/detail/wago-corporation/249-116/13549530
Din rail |  |  | 9 | 2 |  | 18 |  | Digikey | https://www.digikey.no/en/products/detail/american-electrical-inc/TS3575SL/382581
Glands |  |  | 1.7 | 5 |  | 8.5 |  | Digikey | https://www.digikey.no/en/products/detail/amphenol-industrial-operations/AIO-CSM18/3904948
Vents for enclosure |  |  | 4 | 2 |  | 8 |  | Digikey | https://www.digikey.no/en/products/detail/bud-industries/NBX-10911/439513
Large electronics enclosure | PTQ-11070-C |  | 80 | 1 |  | 80 |  | Digikey | https://www.digikey.no/en/products/detail/bud-industries/PTQ-11070-C/13907350
Ferrules 0,75mm2 |  |  |  |  |  | 0 |  | Digikey | https://www.digikey.no/en/products/detail/panduit-corp/FSD76-8-D/448656
Ferrules 1,5mm2 |  |  |  |  |  | 0 |  | Digikey | https://www.digikey.no/en/products/detail/panduit-corp/FSD78-10-D/448661
Ferrules 2,5mm2 |  |  |  |  |  | 0 |  | Digikey | https://www.digikey.no/en/products/detail/american-electrical-inc/11121025/266390
Cable 0,75mm2 |  |  |  |  |  | 0 |  | Digikey | https://www.digikey.no/en/products/detail/te-connectivity-raychem-cable-protection/RL0111-0-75-0/13590776
Cable 2,5mm2 |  |  |  |  |  | 0 |  | Digikey | https://www.digikey.no/en/products/detail/te-connectivity-raychem-cable-protection/RL0111-2-50-0/13590771
Wire duct |  |  | 7 | 1 |  | 7 |  | Digikey | https://www.digikey.no/en/products/detail/essentra-components/RX2525-0/3815065
Wago connector |  |  |  |  |  | 0 |  | Digikey | https://www.digikey.no/en/products/detail/wago-corporation/221-412-VE00-2500/13175703
Zip ties |  |  |  |  |  | 0 |  | Digikey | https://www.digikey.no/en/products/detail/advanced-cable-ties-inc/AL-04-18-0-C/10380578
Zip tie adhesive pads |  |  |  |  | 29 | 29 |  | Digikey | https://www.digikey.no/en/products/detail/essentra-components/23TA00500B/11639606
Electronics and safety total |  |  |  |  |  | 1856.6
Machine feet | Adjustable foot Ø 60 mm M8 x 40 |  | 11 | 6 | 50 | 116 |  | Sorotec | https://www.sorotec.de/shop/product_info.php?info=p9066_adjustable-foot-d60-m8-x-40.html&no_boost=1 | https://www.mcmaster.com/adjustable-feet/adjustability~swivel/mount-type~threaded-stud/thread-size~m8/ | 6111K663 (https://www.mcmaster.com/6111K663)
M6 screw for spindle mount?
M5 16mm screw | 200pcs | M5, Socket, Alloy steel | 16.2 | 2 |  | 32.4 |  | Wuerth |  | https://www.mcmaster.com/screws/system-of-measurement~metric/thread-size~m5/length~16-mm/ | 91290A232
M5 20mm screw | 100pcs | M5, Socket, Alloy steel | 16.4 | 1 |  | 16.4 |  | Wuerth |  | https://www.mcmaster.com/screws/system-of-measurement~metric/thread-size~m5/length~20-mm/ | 91290A242
M5 30mm screw | 10pcs | M5, Socket, Alloy steel | 5.8 | 1 |  | 5.8 |  | Wuerth |  | https://www.mcmaster.com/screws/system-of-measurement~metric/thread-size~m5/length~30mm/ | 91290A194
M5 40mm screw | 100pcs | M5, Socket, Alloy steel | 17.2 | 1 |  | 17.2 |  | Wuerth |  | https://www.mcmaster.com/screws/system-of-measurement~metric/thread-size~m5/length~40mm/ | 90128A257
M5 70mm screw | 100pcs | M5, Socket, Alloy steel | 8.4 | 4 |  | 33.6 |  | Wuerth |  | https://www.mcmaster.com/screws/system-of-measurement~metric/thread-size~m5/length~70mm/ | 91290A272
M5 80mm screw | 10pcs | M5, Socket, Alloy steel
M4 12mm screw | 100pcs | M4, Socket, Alloy steel | 11.5 | 1 |  | 11.5 |  | Wuerth |  | https://www.mcmaster.com/screws/system-of-measurement~metric/thread-size~m4/length~12-mm/ | 91290A148
M4 20mm screw | 200pcs | M4, Socket, Alloy steel | 13.6 | 2 |  | 27.2 |  | Wuerth |  | https://www.mcmaster.com/screws/system-of-measurement~metric/thread-size~m4/length~20-mm/ | 91290A168
M5 set screws for pinions | 12pcs | 10mm length |  |  |  | 0 |  | Wuerth
M5 washers | 100pcs |  |  | 1 |  | 0 |  | Wuerth |  | https://www.mcmaster.com/standard-washers/system-of-measurement~metric/for-screw-size~m5/general-purpose-washers-8/od~10mm/ | 93475A240
M5 nuts | 25pcs
Carriage bolt | 50pcs | 110mm length | 25 | 1 |  | 25 |  | Wuerth | https://nettbutikk.wuerth.no/festemidler/laaseskruer/laaseskruer-m-mutter-4-8-elzink | https://www.mcmaster.com/carriage-bolts/length~4-1-2/thread-size~5-16-18/ | 93548A601
Nuts for carriage bolts | 50pcs |  |  | 1 |  | 13 |  | Wuerth |  | https://www.mcmaster.com/nuts/system-of-measurement~inch/thread-size~5-16-18/hex-nut-profile~standard/medium-strength-steel-hex-nuts-grade-5/ | 95462A030
Washers for carriage bolts | 50pcs |  |  | 1 |  | 7 |  | Wuerth |  | https://www.mcmaster.com/standard-washers/washers-4/for-screw-size~5-16/washer-type~flat/oversized-washers-9/ | 91525A229
Misc milling bits
M4 tap (if not thread milling)
M5 tap (if not thread milling)
M8 tap
Spade drill (for carriage bolt heads)
10-12mm drill (for carriage bolts)
Screw driver
Ferrule crimping pliers |  |  |  | 1 |  |  |  | Digikey | https://www.digikey.no/en/products/detail/molex/2002180700/7066388
Fasteners and misc hardware total |  |  |  |  |  | 305.1
Complete BOM total |  |  |  |  |  | 4550.02

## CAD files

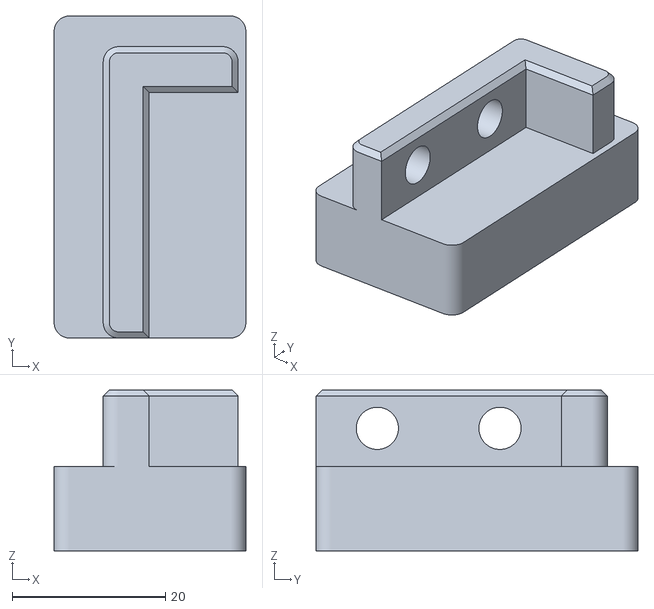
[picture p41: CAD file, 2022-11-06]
files-for-3D-print/z-probe-plate-holder-1pcs.stl
25.0 x 42.0 x 21.0

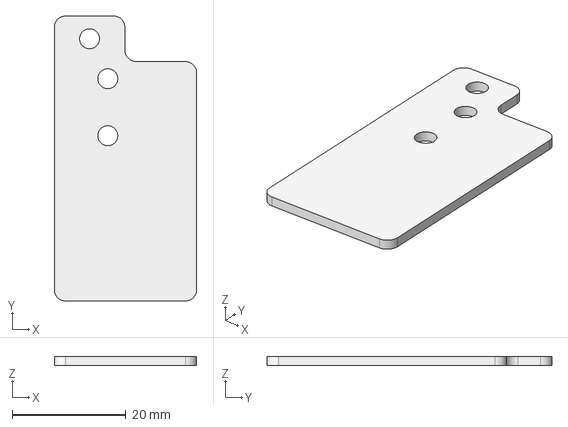
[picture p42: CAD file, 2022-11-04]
files-for-CNC-machining/z-probe-plate-for-pcb-milling.step
25.0 x 50.0 x 1.60 mm

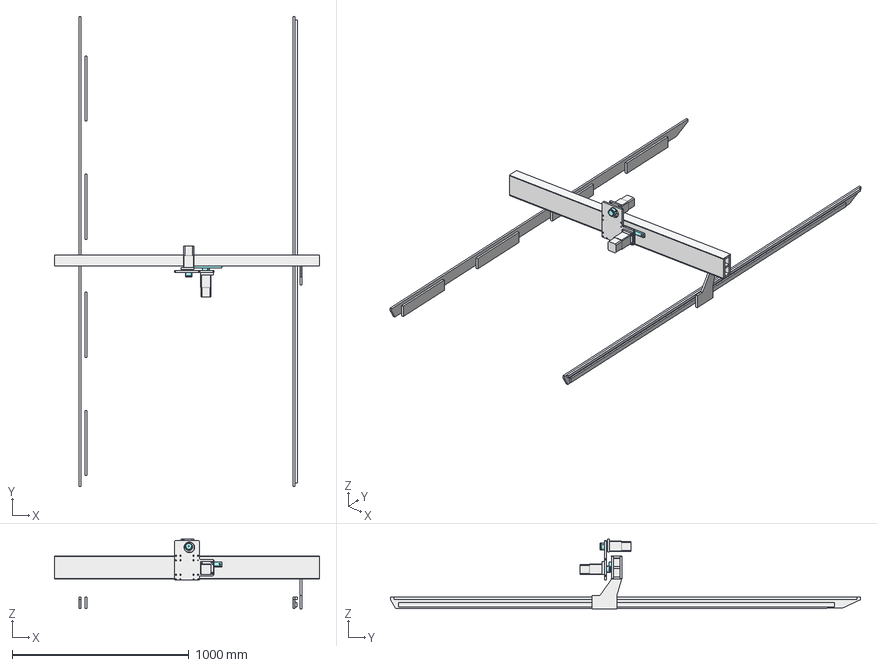
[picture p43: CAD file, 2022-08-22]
humphrey2.FCStd
1500.0 x 2660.0 x 395.2 mm
Core wall - outer
Core wall - outer (Mirror #2)
Inner cross wall pieces (Mirror #3)
Rack Y
Rail Y
Gantry foot wall
Gantry mid plate
Gantry bottom plate
Gantry back plate
Gantry front plate
Gantry top plate
Pinion - Z axis
X axis plate
Gearbox and nema23 motor - Z axis
Pinion - X axis
Gearbox and nema23 motor - X axis
X motor plate
Rack - X axis
X motor plate001

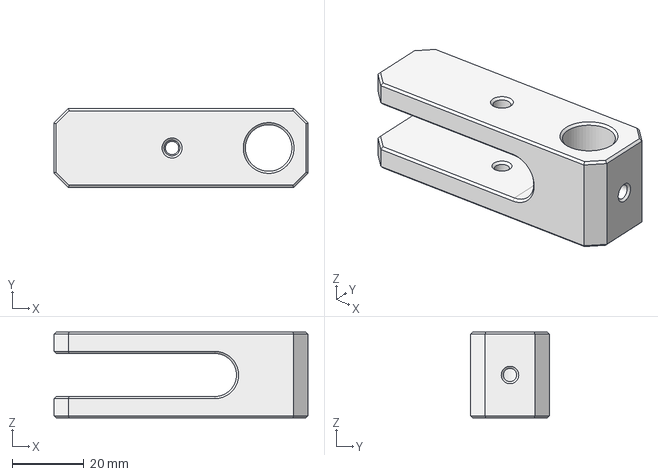
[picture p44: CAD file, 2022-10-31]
spare-parts/marker-holder-for-dust-skirt.FCStd
71.0 x 22.0 x 24.0 mm

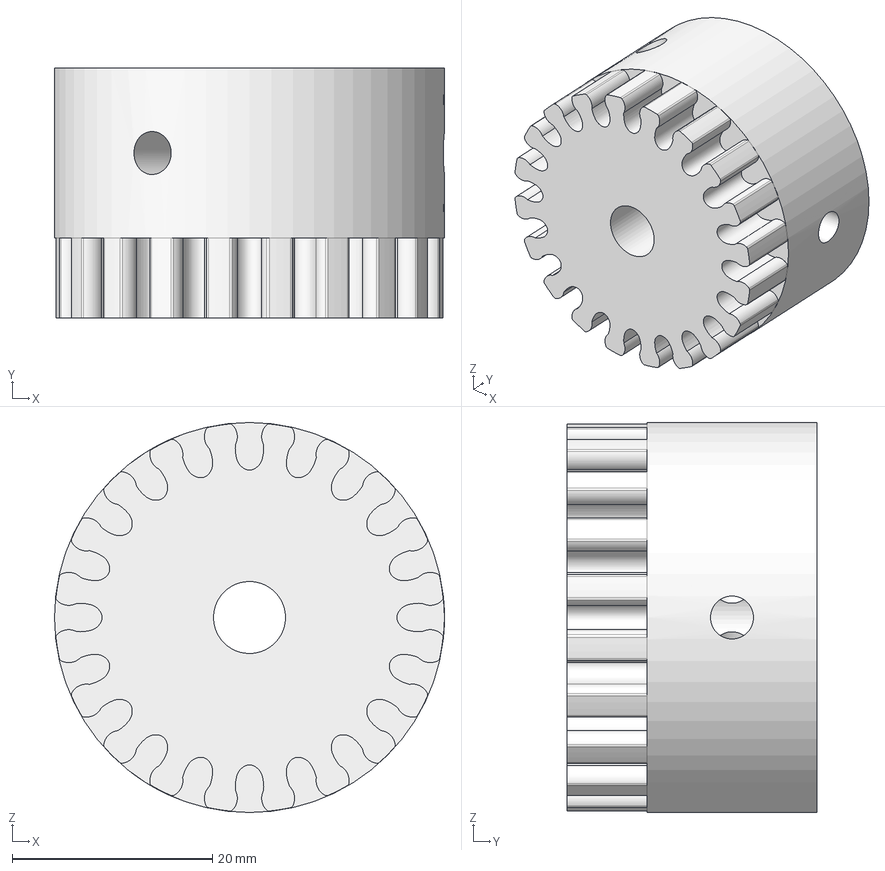
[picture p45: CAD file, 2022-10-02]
step-files-for-cad-import/cnc-friendy-rack-and-pinion-for-humphrey2-Pinion.step
39.0 x 25.0 x 39.0 mm

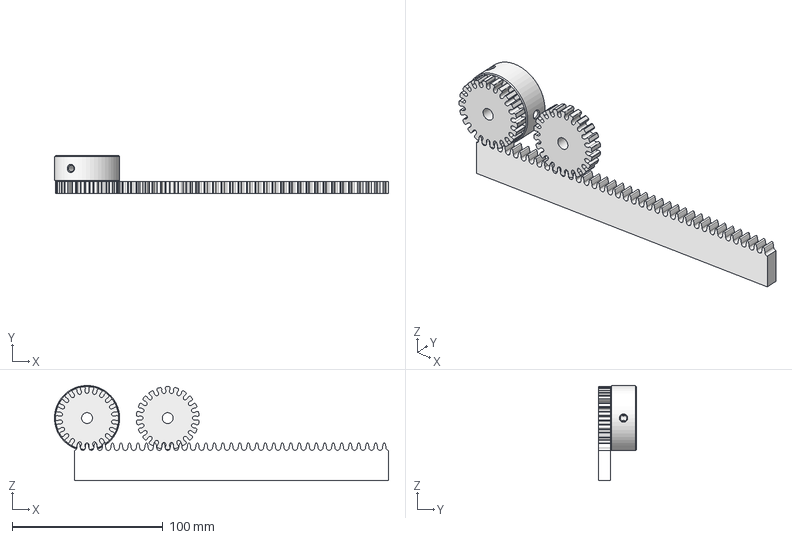
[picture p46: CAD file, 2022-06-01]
cnc-friendy-rack-and-pinion-for-humphrey2.FCStd
221.2 x 25.0 x 62.9 mm
Rack
Pinion - position check
Pinion

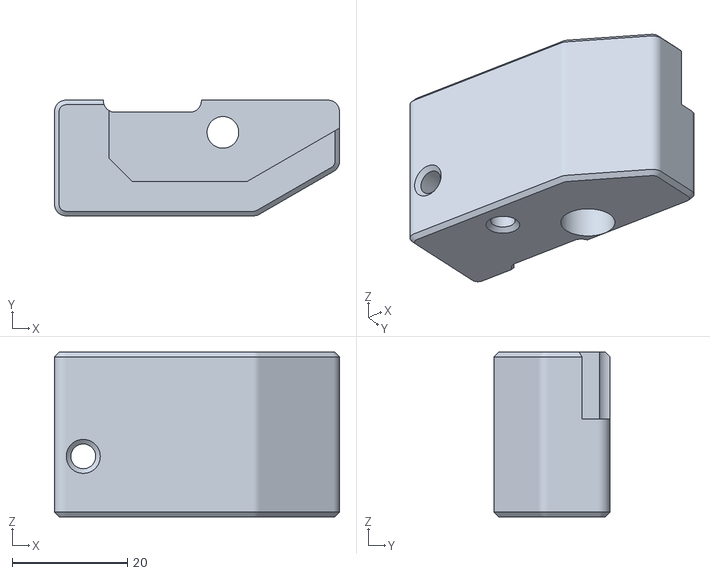
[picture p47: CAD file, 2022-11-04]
files-for-3D-print/end-stop-Y1.stl
49.5 x 20.1 x 28.6

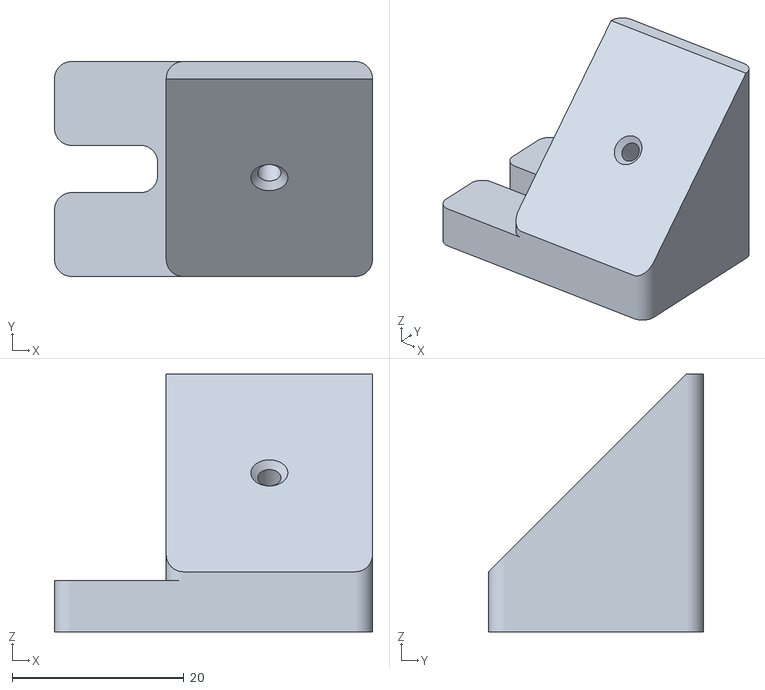
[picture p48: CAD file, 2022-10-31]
spare-parts/blackbox-interface-mount-left.stl
37.0 x 25.0 x 30.0

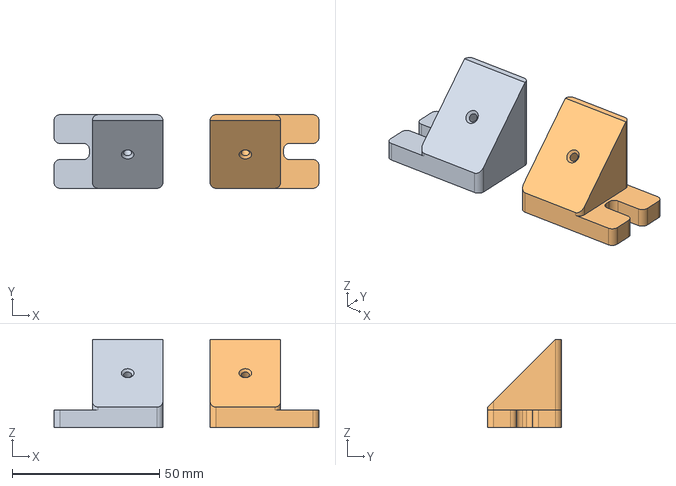
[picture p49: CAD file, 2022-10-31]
spare-parts/blackbox-interface-mount.FCStd
90.0 x 25.0 x 30.0 mm
Body (Mirror #1)

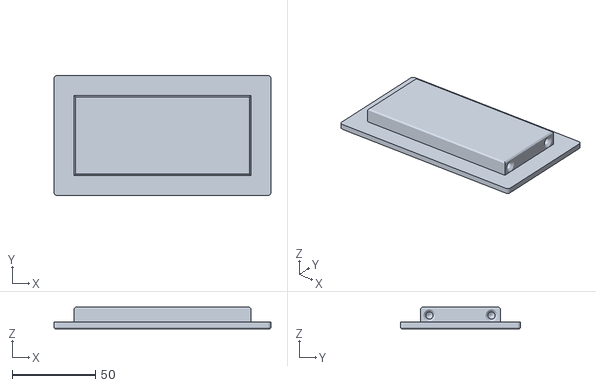
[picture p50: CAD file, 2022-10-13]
files-for-3D-print/end-cap-y2-1pcs.stl
130.0 x 72.0 x 13.0

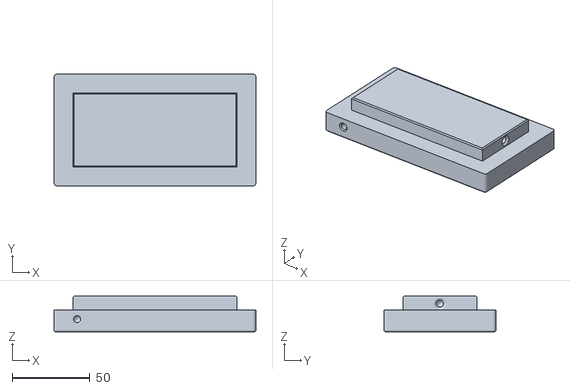
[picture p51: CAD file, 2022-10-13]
files-for-3D-print/end-cap-y1-1pcs.stl
130.0 x 72.0 x 23.0

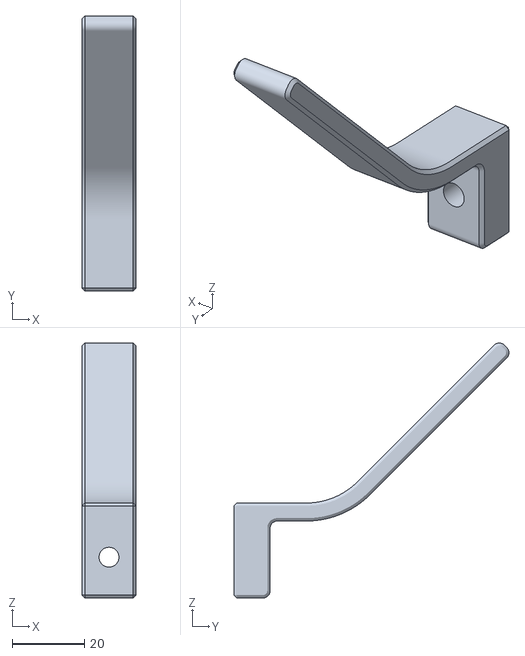
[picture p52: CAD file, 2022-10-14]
spare-parts/dust-hose-holder-open.stl
15.0 x 76.1 x 70.6

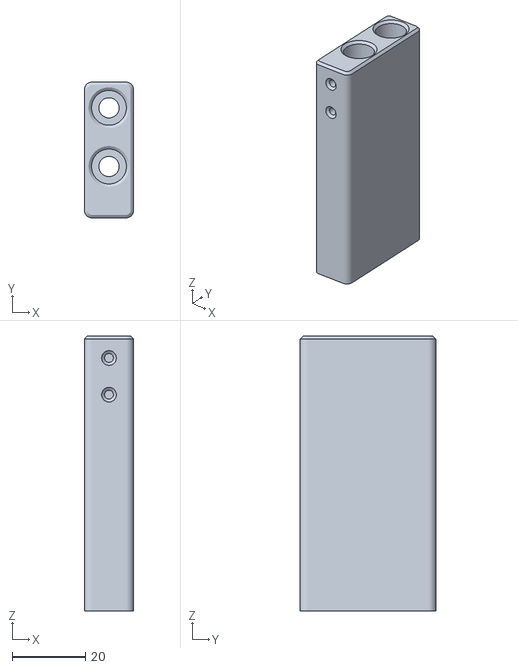
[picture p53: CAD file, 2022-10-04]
files-for-3D-print/e-chain-bracket-x-axis-1pcs.stl
13.4 x 37.0 x 75.0

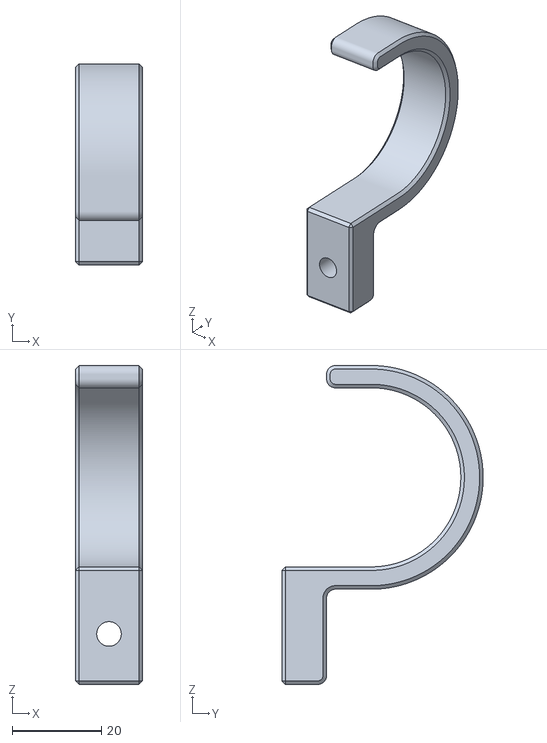
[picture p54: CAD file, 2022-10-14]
spare-parts/dust-hose-holder-closed.stl
15.0 x 45.0 x 71.3

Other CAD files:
files-for-3D-print/end-stop-Y2.stl
spare-parts/blackbox-interface-mount-right.stl
files-for-3D-print/e-chain-bracket-gantry-1pcs.stl
files-for-CNC-machining/z-probe-plate-for-pcb-milling.dxf
spare-parts/marker-holder-for-dust-skirt.stl

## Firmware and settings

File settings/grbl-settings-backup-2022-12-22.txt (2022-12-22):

$0=10.0  ;  Step pulse time, microseconds
$1=255  ;  Step idle delay, milliseconds
$2=0  ;  Step pulse invert, mask
$3=0  ;  Step direction invert, mask
$4=0  ;  Invert step enable pin, boolean
$5=7  ;  Invert limit pins, boolean/mask
$6=1  ;  Invert probe pin, boolean
$7=0  ;  Disable spindle with 0 speed, boolean
$8=0  ;  Ganged axes direction invert as bitfield
$10=511  ;  Status report options, mask
$11=0.010  ;  Junction deviation, millimeters
$12=0.002  ;  Arc tolerance, millimeters
$13=0  ;  Report in inches, boolean
$14=0  ;  Limit pins invert, mask
$15=0  ;  Coolant pins invert, mask
$16=0  ;  Spindle pins invert, mask
$17=0  ;  Control pins pullup disable, mask
$18=0  ;  Limit pins pullup disable, mask
$19=0  ;  Probe pin pullup disable, boolean
$20=0  ;  Soft limits enable, boolean
$21=1  ;  Hard limits enable, boolean
$22=1  ;  Homing cycle enable, boolean (Grbl) / mask (GrblHAL)
$23=3  ;  Homing direction invert, mask
$24=100.0  ;  Homing locate feed rate, mm/min
$25=2000.0  ;  Homing search seek rate, mm/min
$26=250  ;  Homing switch debounce delay, milliseconds
$27=8.000  ;  Homing switch pull-off distance, millimeters
$28=0.100  ;  G73 retract distance, in mm
$29=0.0  ;  Step pulse delay (ms)
$30=1000.000  ;  Maximum spindle speed, RPM
$31=0.000  ;  Minimum spindle speed, RPM
$32=0  ;  Laser-mode enable, boolean
$33=5000.0  ;  Spindle PWM frequency
$34=0.0  ;  Spindle off Value
$35=0.0  ;  Spindle min value
$36=100.0  ;  Spindle max value
$37=0  ;  Stepper deenergize mask
$39=1  ;  Enable printable realtime command characters, boolean
$40=0  ;  Apply soft limits for jog commands, boolean
$43=1  ;  Homing passes
$44=4  ;  Homing cycle 1
$45=3  ;  Homing cycle 2
$46=0  ;  Homing cycle 3
$62=0  ;  Sleep Enable
$63=2  ;  Feed Hold Actions
$64=0  ;  Force Init Alarm
$65=0  ;  Require homing sequence to be executed at startup
$70=7  ;  Network Services
$73=1  ;  Wifi Mode
$74=  ;  Wifi network SSID
$75=  ;  Wifi network PSK
$100=139.130  ;  X-axis steps per millimeter
$101=139.130  ;  Y-axis steps per millimeter
$102=139.130  ;  Z-axis steps per millimeter
$110=9000.000  ;  X-axis maximum rate, mm/min
$111=9000.000  ;  Y-axis maximum rate, mm/min
$112=9000.000  ;  Z-axis maximum rate, mm/min
$120=200.000  ;  X-axis acceleration, mm/sec^2
$121=200.000  ;  Y-axis acceleration, mm/sec^2
$122=200.000  ;  Z-axis acceleration, mm/sec^2
$130=1300.000  ;  X-axis maximum travel, millimeters
$131=2500.000  ;  Y-axis maximum travel, millimeters
$132=200.000  ;  Z-axis maximum travel, millimeters
$300=Grbl  ;  Hostname
$302=192.168.5.1  ;  IP Address
$303=192.168.5.1  ;  Gateway
$304=255.255.255.0  ;  Netmask
$305=23  ;  Telnet Port
$306=80  ;  HTTP Port
$307=81  ;  Websocket Port
$341=0  ;  Tool Change Mode
$342=30.0  ;  Tool Change probing distance
$343=25.0  ;  Tool Change Locate Feed rate
$344=200.0  ;  Tool Change Search Seek rate
$345=100.0  ;  Tool Change Probe Pull Off rate
$370=0  ;  Invert I/O Port Inputs (mask)
$384=0  ;  Disable G92 Persistence

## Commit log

2022-03-20 added early design file and gitignore
    [humphrey2-rough-cad-sketch.FCStd]
2022-03-21 Started work on BOM
    [BOM-Humphrey2.xls]
2022-03-21 Added preview of BOM
2022-03-21 updated bom - clustered costs
    [BOM-Humphrey2.xls]
2022-06-01 Work on test piece and rack and pinion
    [cnc-friendy-rack-and-pinion-for-humphrey2.FCStd, construction-test-piece.FCStd, humphrey2-rough-cad-sketch.FCStd]
2022-06-02 finished first iteration
    [construction-test-piece.FCStd]
2022-06-15 tweaked proportions
    [construction-test-piece.FCStd, humphrey2-rough-cad-sketch.FCStd]
2022-06-15 changed feet to m8
    [BOM-Humphrey2.xls]
2022-06-17 started work on min design
    [humphrey2.FCStd]
2022-06-17 design work
    [humphrey2.FCStd]
2022-06-23 docu of cad process
2022-06-23 cad dev
    [construction-test-piece.FCStd, humphrey2-rough-cad-sketch.FCStd, humphrey2.FCStd]
2022-08-04 design progress
    [humphrey2.FCStd]
2022-08-08 started x axis plate and z axis design
    [humphrey2.FCStd]
2022-08-09 z and x axis progress
    [humphrey2.FCStd]
2022-08-10 z axis progress
    [humphrey2.FCStd]
2022-08-22 Renamed sketch with troublesome constraint
    [humphrey2.FCStd]
2022-08-29 CAD docu update
2022-09-01 Progress with gantry foot
2022-09-02 good gantry progress
2022-09-05 gantry and bed core progress
2022-09-06 bed progress
2022-09-07 designed 3D printed parts
2022-09-09 minor tweaks - improved X homing switch holder
    [construction-test-piece.FCStd]
2022-09-12 deleted old dev file
    [humphrey2-rough-cad-sketch.FCStd]
2022-09-15 added parts for 3D print
    [e-chain-bracket-gantry-1pcs.stl, e-chain-bracket-x-axis-1pcs.stl, end-cap-y1-1pcs.stl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]
2022-09-15 leg sketching
2022-09-20 changed motorplate hole type
2022-10-02 added z probe plate
2022-10-02 started work on spare parts
    [cnc-friendy-rack-and-pinion-for-humphrey2-Pinion.step]
2022-10-04 updated 3D print parts
    [e-chain-bracket-gantry-1pcs.stl, e-chain-bracket-x-axis-1pcs.stl, end-cap-y1-1pcs.stl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]
2022-10-13 tweaked 3d printed parts
    [end-cap-y1-1pcs.stl, end-cap-y2-1pcs.stl]
2022-10-14 added wood sheet holes and hose clamps
    [dust-hose-holder-closed.stl, dust-hose-holder-open.stl]
2022-10-31 add ons
    [blackbox-interface-mount-left.stl, blackbox-interface-mount-right.stl, blackbox-interface-mount.FCStd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]
2022-10-31 docu of first prod and assembly
2022-10-31 added pics from test milling and assembly
2022-11-04 design tweaks
    [end-stop-Y1.stl, end-stop-Y2.stl, z-probe-plate-for-pcb-milling.dxf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]
2022-11-04 fixed fillets
    [z-probe-plate-for-pcb-milling.dxf]
2022-11-06 tweaked z probe height
    [z-probe-plate-holder-1pcs.stl]
2022-11-29 cad tweaks
2022-11-29 updated bom
    [BOM-Humphrey2.xls]
2022-11-30 added bom link
2022-12-02 tweaked bom (wip)
    [BOM-Humphrey2.xls]
2022-12-09 added safety electronics
    [BOM-Humphrey2.xls]
2022-12-19 tweaked bom
    [BOM-Humphrey2.xls]
2022-12-19 added oil for rails
    [BOM-Humphrey2.xls]
2022-12-19 added 80mm M5 screws
    [BOM-Humphrey2.xls]
